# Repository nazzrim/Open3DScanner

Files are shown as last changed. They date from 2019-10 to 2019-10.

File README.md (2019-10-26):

# Open3DScanner
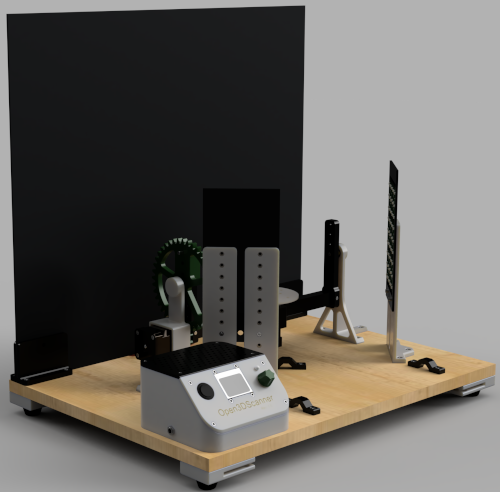
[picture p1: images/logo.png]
The Open3DScanner


The Open3DScanner is an open source photogrammetry 3D Scanner. Despite its name it does not provide you with the full photogrammetry pipeline.

Instead it enables you to automaticall create sets of photos by using your smartphone camera. These photos need to be processed by your normal photogrammetry pipeline later on.

But by automating the process of capturing the required photos the time you need to spend on creating a 3D scan can significantly decreased.

## Features
- Automatic generation of photosets for photogrammetry
- Support for android and iOS devices
- Adjustable scanning parameters for different granularities of detail
- Integrated LED lights to increase illumination of photos
- Removable backplate and storage area below the baseplate for reduces space requirements
- Adjustable scanner frame for differently sized objects
- Extensive documentation, providing you with build instructions and many additional informations about photogrammetry, the design process, and other open source 3D scanners

## License
Since this repository contains mixed resources (code, documents, images, ...) thera are different licenses which apply to different portions of the repository.

For that reason each subfolder of the root folder contains its own LICENSE.md file which defines the license which applies to the corresponding resources.

But in general code and 3D model resources are licensed under the GPLv3 while media resources (like documents and images) are licensed with the CC-BY-SA 4.0 license.

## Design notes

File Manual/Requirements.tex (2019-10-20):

\chapter{Required Parts}%
\label{c:bom}%
This chapter shows which things are needed to build the Open3DScanner. It looks at the components of the printer as well as the tools and devices needed to assemble it.%

It is recommended to read this chapter carefully if you want to build your own Open3DScanner.%

\section{Bill of Materials}%
One of the most important points to build your own Open3DScanner is a bill of materials of the required parts.%

This is contained in the following sections. The complete list is divided into two partial lists. The first one contains all electrical components which can be found on the PCB or are connected to it. The second list contains all further things that are needed to assemble the Open3DScanner.%

\subsection{Electrical Components}%
The following table contains all electrical components required to build the Open3DScanner.%

In addition to the component and the required quantity, the identifier of the respective component on the circuit board is also specified. In addition to this, information is given for individual components, which must be considered when purchasing.%

\begin{table}[ht!]%
	\begin{centered}%
		\rowcolors{2}{tableLineTwo}{tableLineOne}% specify rowcolors in tabularx style
		\begin{tabularx} {\linewidth} {>{\rowmac \hsize=1.4\hsize}X>{\rowmac \hsize=0.3\hsize}X>{\rowmac \hsize=0.6\hsize}X>{\rowmac \hsize=1.7\hsize}X<{\clearrow}}%
			\tabularxHeader%
			Component & Quantity & PCB-Identifier  & Note\\%
			\hrefIdx{https://www.espressif.com/en/products/hardware/esp32-devkitc/overview}{ESP32-DevKitC} & 1 & A1 & While I use the \hrefIdx{https://www.az-delivery.de/products/esp32-developmentboard}{AZ-Delivery ESP32-DevKitC}, any version that meets the \hrefIdx{https://www.espressif.com/en/products/hardware/esp32-devkitc/overview}{ESP32-DevKitC} specification should work.\\%
			\hrefIdx{https://www.pololu.com/product/1182}{A4988 Stepper Driver} & 2 & A2TT1 \& A3RT1 & Any A4988 steper driver should work. I recommend getting matching heat sinks.\\%
			\hrefIdx{https://reprap.org/wiki/NEMA\_17\_Stepper\_motor}{Nema 17 Stepper Motor} & 2 & M1RT1 \& M2TT1 & Make sure to buy the version with D-shaft. I use strong stepper motors, like this \hrefIdx{https://www.omc-stepperonline.com/nema-17-stepper-motor/nema-17-bipolar-59ncm-84oz-in-2a-42x48mm-4-wires-w-1m-cable-and-connector-full-d-cut-shaft.html}{\SI{59}{\newton\centi\meter} Nema 17 stepper motor}.\\%
			\hrefIdx{https://www.analog.com/en/products/lt1086.html}{LT1086CT-5} & 1 & U2 & Ensure to get the \hrefIdx{https://www.centralsemi.com/PDFS/CASE/TO\_220\_PD.PDF}{TO-220} type.\\%
			\hrefIdx{https://www.infineon.com/cms/en/product/power/mosfet/12v-300v-n-channel-power-mosfet/irlb8721/}{IRLB 8721} & 1 & Q1 & Ensure to get the \hrefIdx{https://www.centralsemi.com/PDFS/CASE/TO\_220\_PD.PDF}{TO-220} type.\\%
			TO-220 Heatsink & 2 & Q1 \& U2 & I highly recommend at least one for the \hrefIdx{https://www.analog.com/en/products/lt1086.html}{LT1086CT-5} since it gets very hot during operation. The one for the \hrefIdx{https://www.infineon.com/cms/en/product/power/mosfet/12v-300v-n-channel-power-mosfet/irlb8721/}{IRLB 8721} is just to be safe. While I am using the \hrefIdx{https://www.fischerelektronik.de/web\_fischer/en\_GB/heatsinks/C02/Attachable\%20heatsink/PG/FK245MI247O/search.xhtml}{FK 245 MI 247 O} you can choose whatever fits in the space (about \SI{22.5}{\milli\meter}$\times$\SI{10}{\milli\meter}).\\%
			\SI{1}{\milli\litre} Thermal Paste & 1 & - & Required for a good connection between \hrefIdx{https://www.centralsemi.com/PDFS/CASE/TO\_220\_PD.PDF}{TO-220} components and their heatsink. Only a tiny amount is required.\\%
			\hrefIdx{https://www.alps.com/prod/info/E/HTML/Encoder/Incremental/EC12E/EC12E\_list.html}{STEC12E08 Rotary Encoder} & 1 & - & This will be connected to the pin header SW1.\\%
			\hrefIdx{https://www.sparkfun.com/products/10168}{Nokia 5110 Display} & 1 & - & This will be connected to the pin header DS1. Buy one with screw holes. Hole distance on x-axis should be \SI{34}{\milli\meter} and \SI{40.5}{\milli\meter} on the y-axis.\\%
			\SI{5}{\milli\meter} 3-Pin Bi-Color LED & 1 & - & This will be connected to the pin header D1. I recommend using a red-green one.\\%
			\SI{5}{\meter}$\times$\SI{8}{\milli\meter} 300 LED 3528 Strip, \SI{12}{\volt} \SI{1.5}{\ampere} & 1 & - & This will be connected to the pin headers D2, D3, D4, D5.\\%
			Round \SI{20}{\milli\meter} SPST Rocker Switch (R13 112) & 1 & - & This will be connected to the pin header SW2.\\%
			\SI{5.5}{\milli\meter}$\times$\SI{2.1}{\milli\meter} Female DC Power Jack Panel Mount (L722AS) & 1 & - & This will be connected to the pin header SW2. Make sure to grab one with threads and a nut for panel mounting.\\%
			\SI{473}{\nano\farad} Ceramic Capacitor & 1 & C3 & Choose \SI{2.54}{\milli\meter} pin distance and \SI{3.4}{\milli\meter} radius.\\%
			\SI{10}{\micro\farad} Electrolytic Capacitor & 1 & C1 & Choose \SI{2}{\milli\meter} pin distance and \SI{4}{\milli\meter} radius.\\%
			\SI{100}{\micro\farad} Electrolytic Capacitor & 3 & C2, C4, C5 & Choose \SI{2.5}{\milli\meter} pin distance and \SI{6.3}{\milli\meter} radius.\\%
			\SI{100}{\ohm} Resistor & 3 & R1, R2, R6 & Choose whatever you have at hand, like carbon film or metal (oxide) film.\\%
			\SI{330}{\ohm} Resistor & 1 & R4 & Choose whatever you have at hand, like carbon film or metal (oxide) film.\\%
			\SI{10}{\kilo\ohm} Resistor & 2 & R3, R5 & Choose whatever you have at hand, like carbon film or metal (oxide) film.\\%
		\end{tabularx}%
		\caption{BOM for all electrical components of the Open3DScanner --- Part 1/3}%
	\end{centered}%
\end{table}%
\begin{table}[ht!]%
	\begin{centered}%
		\rowcolors{2}{tableLineTwo}{tableLineOne}% specify rowcolors in tabularx style
		\begin{tabularx} {\linewidth} {>{\rowmac \hsize=1.4\hsize}X>{\rowmac \hsize=0.3\hsize}X>{\rowmac \hsize=0.6\hsize}X>{\rowmac \hsize=1.7\hsize}X<{\clearrow}}%
			\tabularxHeader%
			Component & Quantity & PCB-Identifier  & Note\\%
			\hrefIdx{https://www.sparkfun.com/products/8432}{2-Pin Screw Terminals 5mm Pitch} & 7 & J1, J2, SW2, D2, D3, D4, D5 & Take care to get the ones with 5mm pitch.\\%
			\SI{2.54}{\milli\meter} 40-Pin Header & 1 & M1RT1, M2TT2, D1, DS1, SW1 & Will be cut into 1$\times$3, 2$\times$4, 1$\times$5, and 1$\times$8.\\%
			\SI{2.54}{\milli\meter} 40-Pin Socket & 2 & A1, A2TT1, A3RT1 & Will be cut into 2$\times$19 and 4$\times$8. Each cut results in one socket loss.\\%
			1$\times$3 Dupont Housing & 4 & - & Will be used to connect D1 with the bi-color LED on both sides as well as the STEC12E08 rotary encoder on component side.\\%
			1$\times$5 Dupont Housing & 1 & - & Will be used to connect SW1 with the rotary encoder on PCB side.\\%
			1$\times$8 Dupont Housing & 2 & - & Will be used to connect DS1 with the LCD on both sides.\\%
			Female Dupont Terminals & 33 & - & Required for all Dupont housings.\\%
			Molex crimp housing --- Micro-Fit - 1x2-pin, male (430200201) & 4 & - & Required for connecting the lights to the Open3DScanner. Part number \hrefIdx{https://www.molex.com/molex/products/datasheet.jsp?part=active/0430200201\_CRIMP\_HOUSINGS.xml}{Molex 430200201}\\%
			Molex crimp housing --- Micro-Fit - 1x2-pin, female & 4 & - & Required for connecting the lights to the Open3DScanner. Part number \hrefIdx{https://www.molex.com/molex/products/datasheet.jsp?part=active/0430250200\_CRIMP\_HOUSINGS.xml}{Molex 430250200}\\%
			Molex crimp contact --- Micro-Fit, female  & 8 & - & Required for connecting the lights to the Open3DScanner. Part number \hrefIdx{https://www.molex.com/molex/products/datasheet.jsp?part=active/0430300007\_CRIMP\_TERMINALS.xml}{Molex 430300007}\\%
			Molex crimp contact --- Micro-Fit, male  & 8 & - & Required for connecting the lights to the Open3DScanner. Part number \hrefIdx{https://www.molex.com/molex/products/datasheet.jsp?part=active/0430310007\_CRIMP\_TERMINALS.xml}{Molex 430310007}\\%
			Cable Lug & 4 & - & The cable lugs have to match your power jack and your rocker switch. For me it is 2$\times$\SI{2.8}{\milli\meter} (power jack) and 2$\times$\SI{4.8}{\milli\meter} (rocker switch).\\%
			Power Supply \SI{12}{\volt}, \SI{2250}{\milli\ampere} with \SI{5.5}{\milli\meter}$\times$\SI{2.1}{\milli\meter} male Barrel Jack & 1 & - & This will power the whole Open3DScanner\\%
			\SI{15}{\centi\meter} Micro USB-B cable & 1 & - & Used to connect J2 with the ESP32's usb port. Get an already prepared cable if you can, otherwise you need to cut one yourself.\\%
			AWG 18 or \SI{0.75}{\milli\meter\squared} cable & - & - & Used for transmitting power (e.g. from power jack to PCB, within pieces of the LED strip, and towards the LED strip). Since the cables are not exposed to any or only little movement, no special requirements like silicone cables exist. I use simple speaker cable which is sold in rolls of \SI{25}{\meter}. I cannot provide an accurate required quantity for the wires since it depends somewhat on individual wiring.\\%
		\end{tabularx}%
		\caption{BOM for all electrical components of the Open3DScanner --- Part 2/3}%
	\end{centered}%
\end{table}%
\begin{table}[ht!]%
	\begin{centered}%
		\rowcolors{2}{tableLineTwo}{tableLineOne}% specify rowcolors in tabularx style
		\begin{tabularx} {\linewidth} {>{\rowmac \hsize=1.4\hsize}X>{\rowmac \hsize=0.3\hsize}X>{\rowmac \hsize=0.6\hsize}X>{\rowmac \hsize=1.7\hsize}X<{\clearrow}}%
			\tabularxHeader%
			Component & Quantity & PCB-Identifier  & Note\\%
			AWG 24 or \SI{0.2}{\milli\meter\squared} cable & - & - & Used to connect the various components to the PCB. I cannot provide an accurate required quantity for the wires since it depends somewhat on individual wiring.\\%
			PCB & 1 & - & The Gerber files for the PCB of the Open3DScanner are part of this project and can be used to get PCBs from a manufacturer.\\%
		\end{tabularx}%
		\caption{BOM for all electrical components of the Open3DScanner --- Part 3/3}%
	\end{centered}%
\end{table}%

\subsection{Other Components}%
The previous section contains the BOM for all electrical parts of the Open3DScanner.%

In addition, this section contains a BOM for all remaining parts needed to build the Open3DScanner. The separation should help to better bundle the orders with the respective suppliers.%

It should be noted that the quantities specified for the screws indicate maximum quantities. These can be smaller, e.g. if the maximum of four lights are not mounted.%

\begin{table}[ht!]%
	\begin{centered}%
		\rowcolors{2}{tableLineTwo}{tableLineOne}% specify rowcolors in tabularx style
		\begin{tabularx} {\linewidth} {>{\rowmac \hsize=1.2\hsize}X>{\rowmac \hsize=0.3\hsize}X>{\rowmac \hsize=1.5\hsize}X<{\clearrow}}%
			\tabularxHeader%
			Component & Quantity & Note\\%
			\SI{400}{\milli\meter} $\times$ \SI{550}{\milli\meter} $\times$ \SI{16}{\milli\meter} Wooden Board & 1 & This will be used as the base of the whole Open3DScanner\\%
			\SI{500}{\milli\meter} $\times$ \SI{550}{\milli\meter} $\times$ \SI{3}{\milli\meter} PVC Rigid Foam Sheet & 1 & The rear panel of the Open3DScanner.\\%
			\SI{800}{\gram} Roll ABS Filament & 1 & Main color. Other materials like PLA may be fine.\\%
			\SI{800}{\gram} Roll ABS Filament & 1 & Secondary color. Other materials like PLA may be fine.\\%
			\SI{800}{\gram} Roll ABS Filament & 1 & Accent color. Other materials like PLA may be fine.\\%
			Nema 17 Damper & 2 & For decoupling the motors from the Open3DScanner's structure.\\%
			Liquid Glue & 1 & Required for assembling the lights if the M3 tape which is applied to the LED strip does not hold and to glue some nuts in place.\\%
			\SI{5}{\milli\meter} $\times$ \SI{26}{\milli\meter} Steel Rod & 5 & Used to connect and secure various parts.\\%
			625ZZ Bearing & 2 & Used to connect the moving parts to the frame with as little friction as possible.\\%
		\end{tabularx}%
		\caption{BOM for all non-electrical components of the Open3DScanner 1/2}%
	\end{centered}%
\end{table}%

\begin{table}[ht!]%
	\begin{centered}%
		\rowcolors{2}{tableLineTwo}{tableLineOne}% specify rowcolors in tabularx style
		\begin{tabularx} {\linewidth} {>{\rowmac \hsize=1.2\hsize}X>{\rowmac \hsize=0.3\hsize}X>{\rowmac \hsize=1.5\hsize}X<{\clearrow}}%
			\tabularxHeader%
			Component & Quantity & Note\\%
			M3$\times$6 SHCS & 6 & Used to connect the stepper motors to the dampers as well as the LED to the housing.\\%
			M3$\times$8 SHCS & 12 & Used for various connections.\\%
			M3$\times$10 SHCS & 12 & Used for various connections.\\%
			M3$\times$12 SHCS & 6 & Used for various connections.\\%
			M3$\times$20 SHCS & 4 & Used for various connections.\\%
			M3 Nut & 40 & Used for assembling the lights.\\%
			4.0$\times$16 Countersunk Wood Screw & 56 & Used to connect the individual parts with the base.\\%
			5/8'' Rubber Seal Ring & 1 & Used for the stepper driver cable entry in the housing.\\%
			\SI{30}{\milli\meter} $\times$ \SI{15}{\milli\meter} Rubber Feet & 4 & Used as feet for the Open3DScanner.\\%
		\end{tabularx}%
		\caption{BOM for all non-electrical components of the Open3DScanner 2/2}%
	\end{centered}%
\end{table}%

\section{Used Tools}%
Various tools are required to set up the Open3DScanner. These are described in this section.%

At first the standard tools are listed, which are needed, but are not described in this chapter. Screwdrivers are needed for the used screws and even if pliers and tweezers are not absolutely necessary, they prove to be useful in some parts of the assembly.%

\subsection{3D Printer}%
A 3D printer is needed to print all the models from which the Open3DScan-ner is built. The requirements are relatively low as all parts can be printed from PLA or ABS\marginInfo[Used Filaments]{I printed all parts for the Open3DScanner with ABS, so it's the only material I can say for sure that it works. However, it should be possible to use PLA and PETG, as well as other materials, as there are no special forces acting on the parts.}.%

All parts have been designed to fit in the print volume of an \hrefIdx{https://www.prusa3d.com/original-prusa-i3-mk3/}{Original Prusa i3 MK3}, which has a print volume of \SI{250}{\milli\meter} $\times$ \SI{210}{\milli\meter} $\times$ \SI{210}{\milli\meter}. Any other FDM 3D printer can be used, which has at least this print volume. The only thing I am recommending is a heated printing bed, but nowadays it is included in almost all printers.%

\subsection{Crimping Tools}%
In order to achieve a decent and secure wiring of the Open3DScanner, it is necessary to crimp the cables.%

Different crimping tools are used for the different connections. A ferrule crimper is used for the connections to the screw terminals, a universal crimping tool\marginTips[Universal Crimper]{While I mostly bought cheap sets for my crimping tools, I bought an \hrefIdx{http://www.engineer.jp/en/products/pa09e.html}{Engineer PA-09} for crimping Dupont cables, because I crimp such cables most often. Even if this crimping tool is a bit more expensive than comparable crimping pliers, the quality of the crimping tool pays off. For this reason I recommend the \hrefIdx{http://www.engineer.jp/en/products/pa09e.html}{Engineer PA-09}, especially if you frequently crimp Dupont cables.} is used for the dupont cables, which connect the individual components to the board, and a terminal crimp tool is used for the connections to individual components, which have plugs for cable lugs.%

\subsection{Soldering Iron}%
A soldering iron is required to assemble the board. Since the Open3DScan-ner does not use any particularly sensitive or otherwise special parts, almost any soldering iron can be used. It is not necessary to use a digital soldering station.%

\section{Hardware for Photogrammetry}%
A powerful computer shortens the necessary processing time for the photogrammetry process. As already mentioned in chapter~\ref{sec:photogrammetry}, a Nvidia GPU is required to use the Meshroom software. Other photogrammetry software may not require a Nvidia GPU.%

Otherwise, photogrammetry software benefits greatly from more RAM, which is why \SI{32}{\giga\byte} is a reasonable lower limit, which is also mentioned by various manufacturers of software for photogrammetry.%

A further important point that must be considered is that during the calculation large amounts of data are generated in the individual intermediate steps, which have to be persisted. The size of the generated data exceeds the size of the input images by a multiple. One of my example scans with 231 images generated over \SI{20}{\giga\byte}\marginInfo[Example Scan]{The mentioned scan consists of four individual scans, whose data were combined. At this point we do not want to go into further detail regarding this scan, corresponding information can be found in the chapters~\ref{c:userGuide} and~\ref{c:performingScans}.} of data.%

For this reason it must be ensured that sufficiently large amounts of storage space are available.%

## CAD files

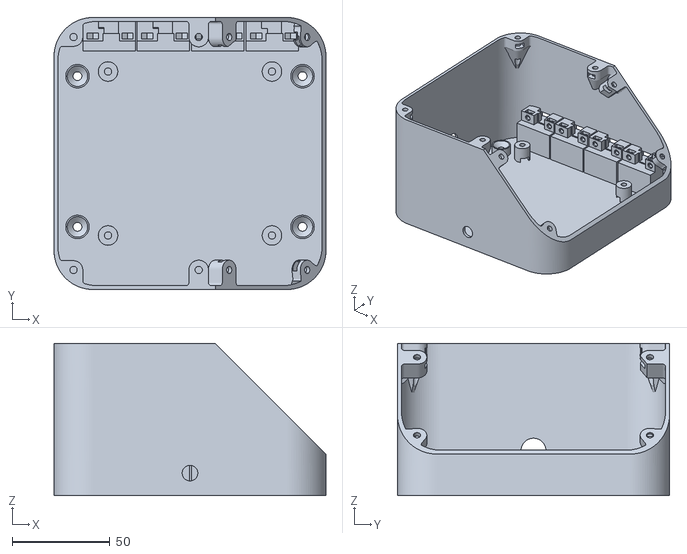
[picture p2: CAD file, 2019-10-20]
STLs/Housing/Housing-Main_v1.stl
139.1 x 139.1 x 77.8

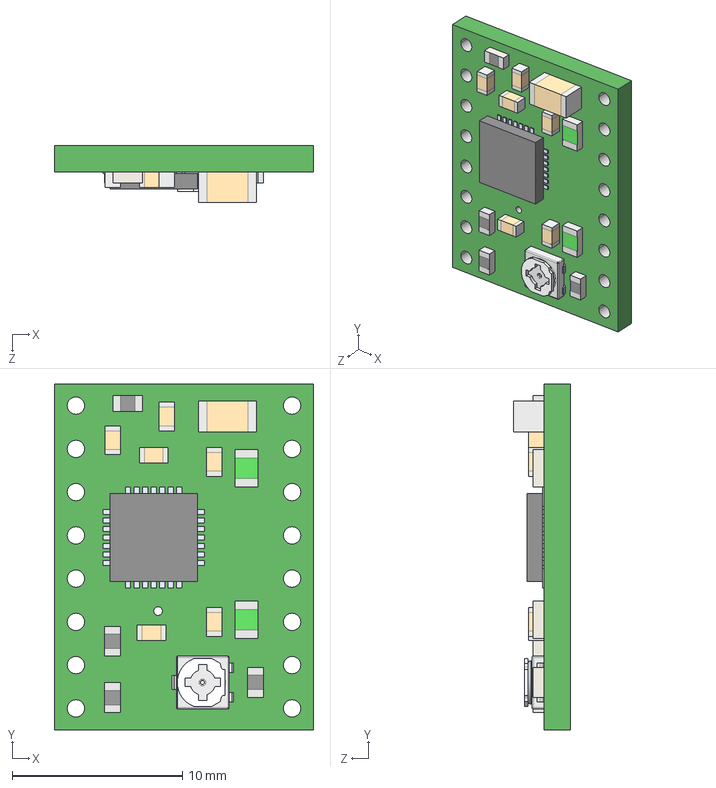
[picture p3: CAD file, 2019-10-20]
PCB/3D Models/a4988-stepper-motor-driver-carrier.step
15.2 x 20.3 x 3.37 mm

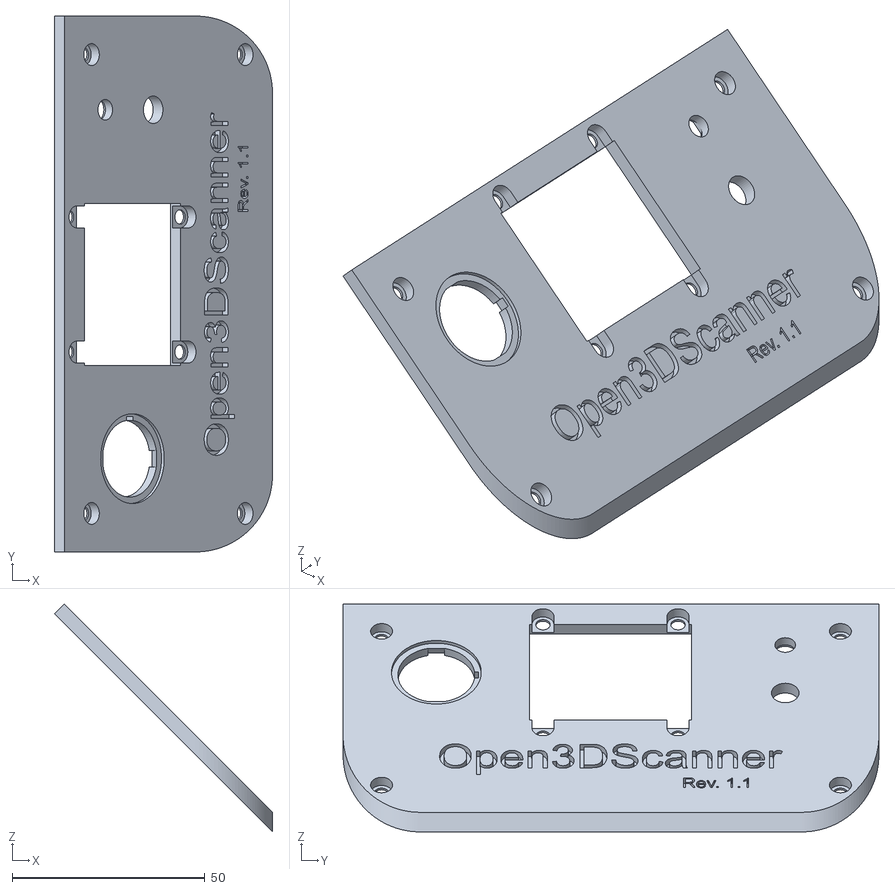
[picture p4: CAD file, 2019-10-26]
STLs/Housing/Housing-Plate_v1.stl
56.6 x 139.1 x 59.1

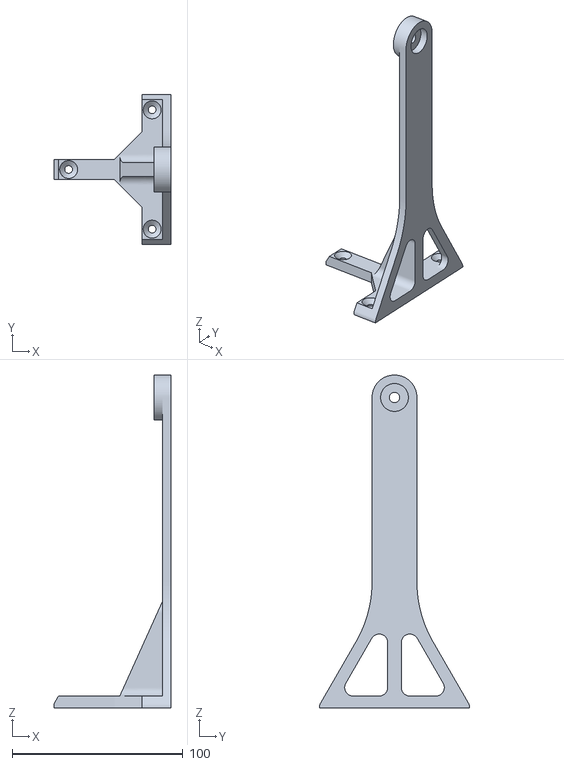
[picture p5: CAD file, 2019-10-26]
STLs/Passive-Stand_v1.stl
68.5 x 88.1 x 195.2

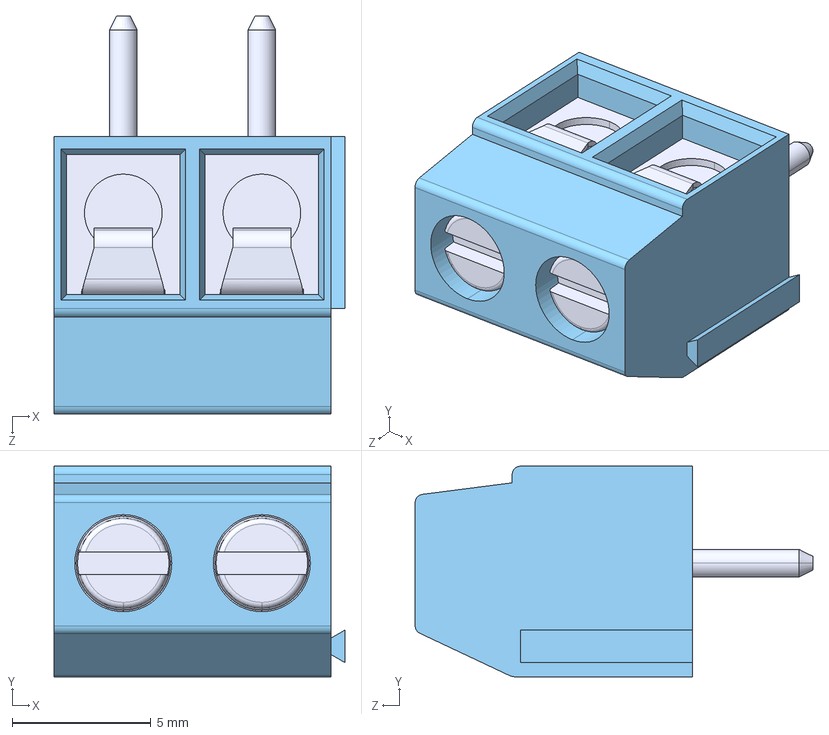
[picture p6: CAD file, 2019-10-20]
PCB/3D Models/CUI_TB002-500-02BE.step
10.5 x 7.60 x 14.4 mm

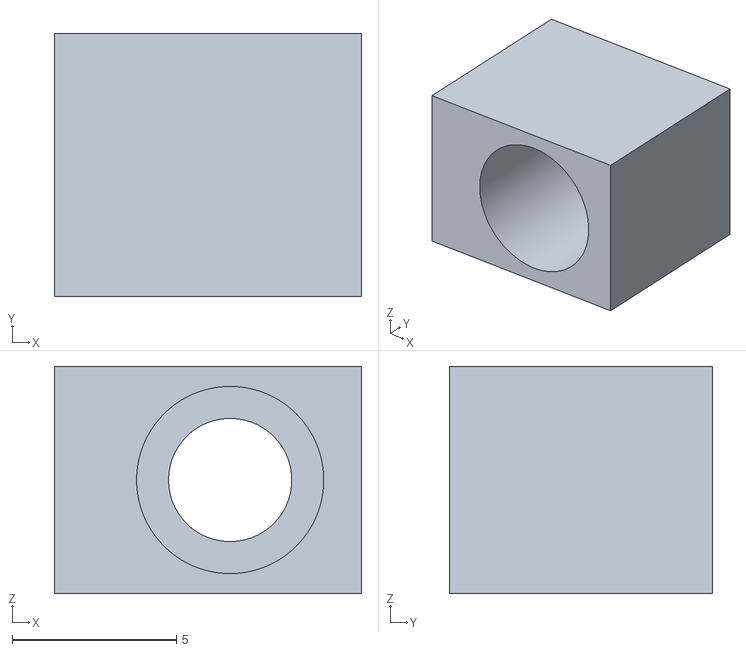
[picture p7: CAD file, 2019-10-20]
STLs/Housing/MicroFit-Holder-P2_v1.stl
9.35 x 8.00 x 6.93

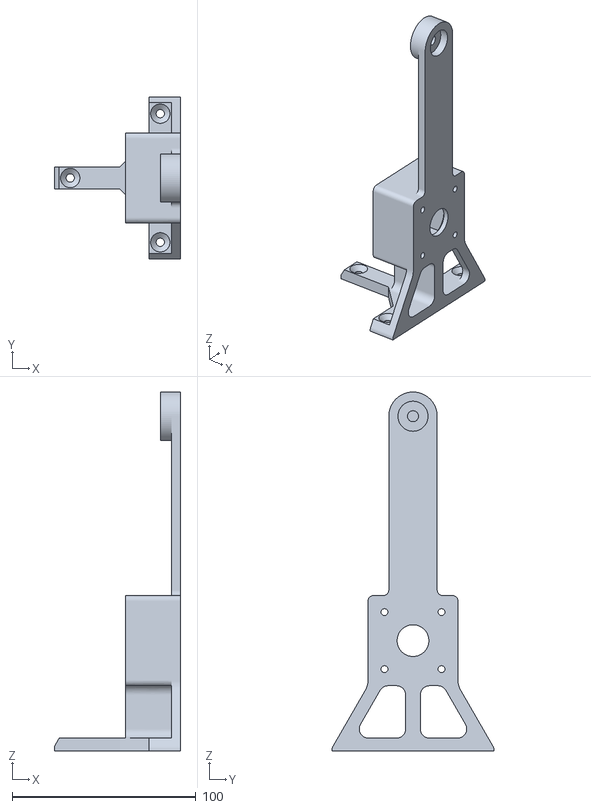
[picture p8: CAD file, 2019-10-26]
STLs/Rotor-Stand_v1.stl
68.5 x 88.1 x 195.2

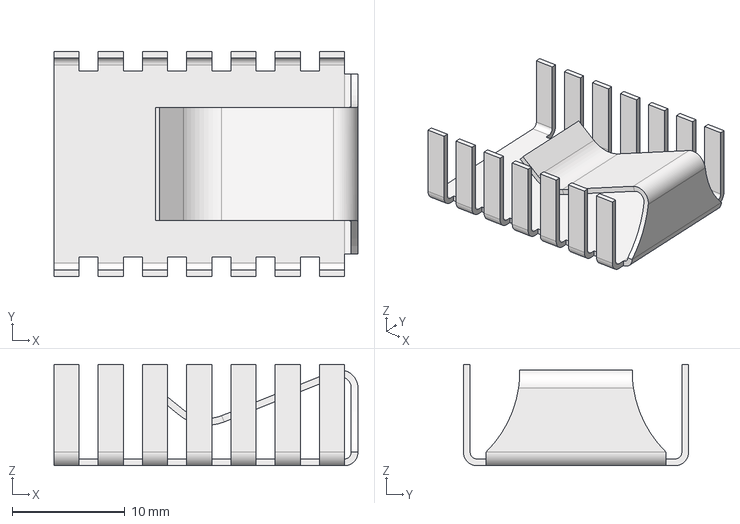
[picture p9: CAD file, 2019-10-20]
PCB/3D Models/fk_245_mi_247_o.stp
27.0 x 20.0 x 9.00 mm

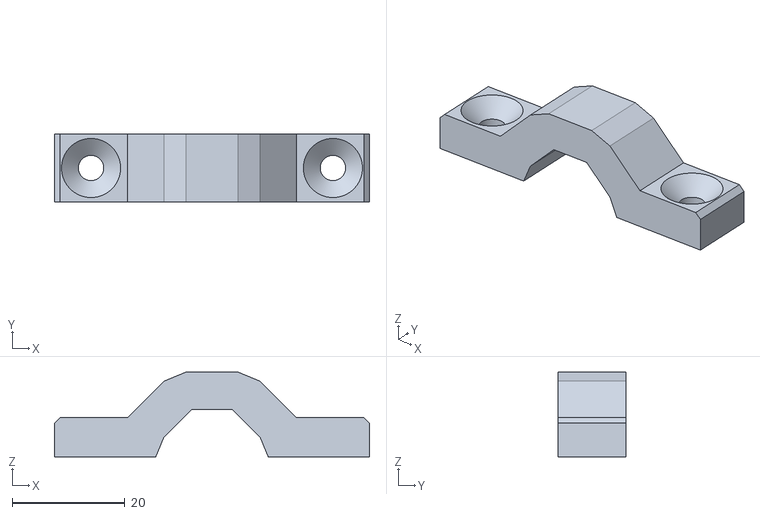
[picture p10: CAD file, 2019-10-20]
STLs/Cable-Holder_v1.stl
56.0 x 12.0 x 15.1

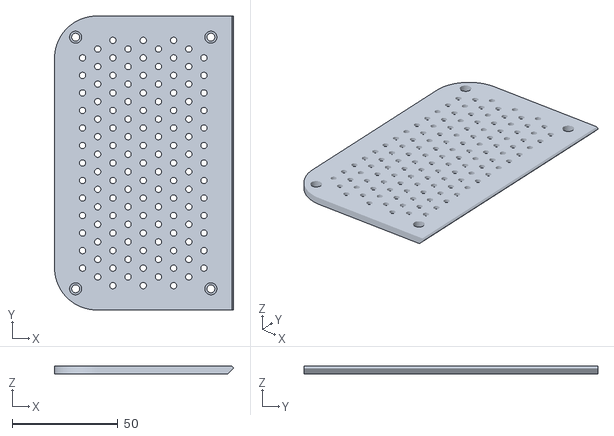
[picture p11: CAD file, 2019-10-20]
STLs/Housing/Housing-Top_v1.stl
84.7 x 139.1 x 3.60

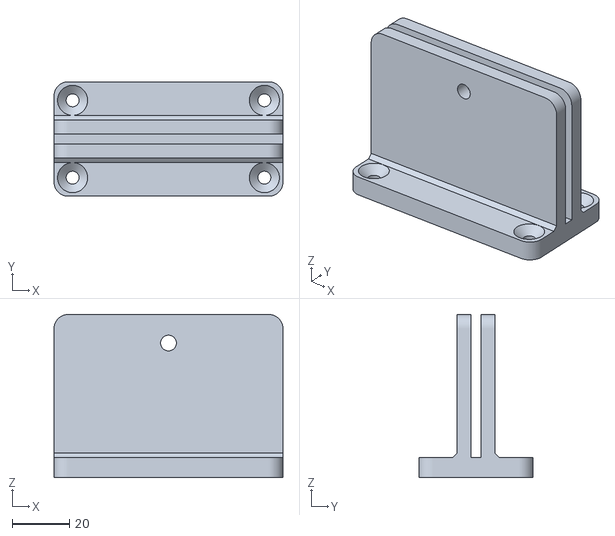
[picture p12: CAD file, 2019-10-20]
STLs/Backplate-Holder_v1.stl
80.0 x 40.0 x 57.0

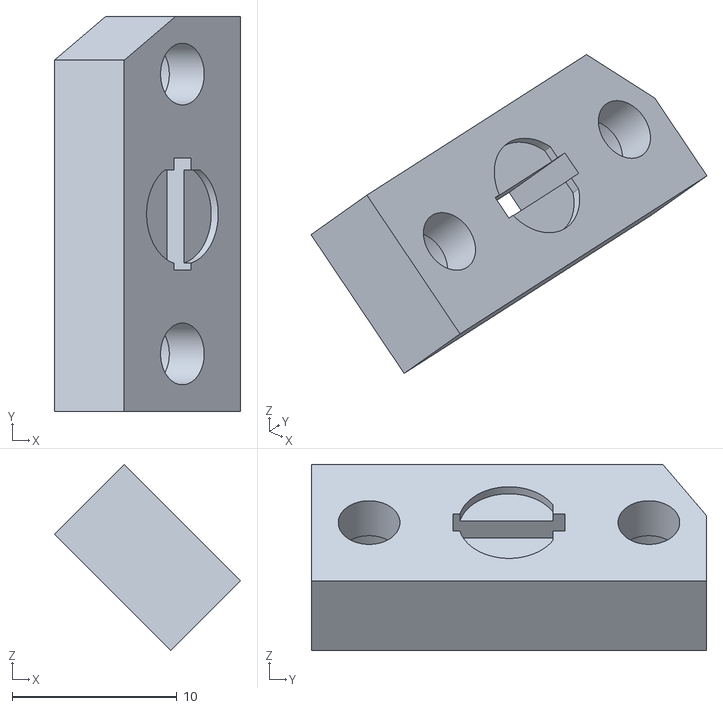
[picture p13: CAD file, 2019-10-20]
STLs/Housing/LED-Holder_v1.stl
11.3 x 24.0 x 11.3

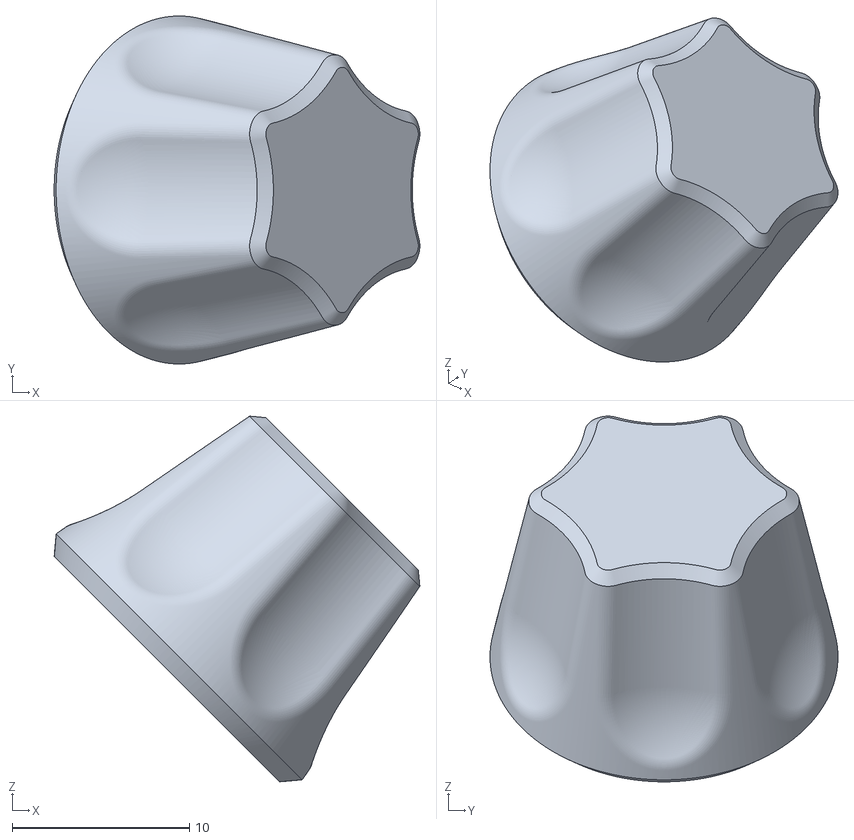
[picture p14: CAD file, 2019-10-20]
STLs/Housing/Knob_v1.stl
20.7 x 19.7 x 20.7

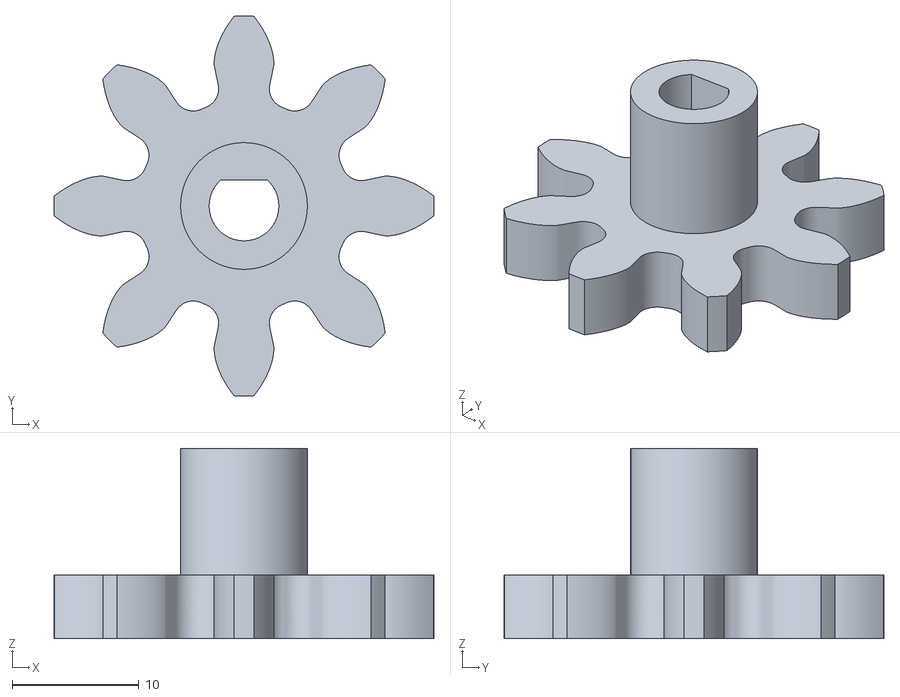
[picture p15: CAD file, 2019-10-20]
STLs/Rotor-Pinion_v1.stl
30.0 x 30.0 x 15.0

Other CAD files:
STLs/Rotor-Arm_v1.stl
STLs/Housing/Encoder-Holder_v1.stl
STLs/Turntable-Arm_v1.stl
STLs/Housing/LCD-Holder_v1.stl
STLs/Foot-Holder-Clamp_v1.stl
STLs/Housing/MicroFit-Holder-P1_v1.stl
STLs/Rotor-Gear_v1.stl
STLs/Spotligt-Frame_v1.stl
STLs/Spotligt-Stand_v1.stl
STLs/Turntable-Medium_v1.stl

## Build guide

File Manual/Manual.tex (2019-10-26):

\documentclass[a4paper]{yReport}%

\usepackage{fontawesome5}% Required by yAuthorBlock
\usepackage{yAuthorBlock}% Used to create the author block on page 2
\usepackage{tabularx}% Since tabu (used by yReport) is not behaving the expected way, use tabularx
\usepackage[binary-units=true]{siunitx}% Used to display numbers and units in a proper way
\usepackage{indextools}% Used to build a href list for printed documents
\usepackage{xparse}% Required for string magic to display urls in index a proper way
\usepackage{infoBulle}% Necessary to display the info/warn/... blocks in the main area
\usepackage{marginInfoBulle}% Necessary to display the info/warn/... blocks in the margin area
\usepackage[cleanlook, english, TeX]{isodate}% Used for uniform displaying dates. Required because of strange behaviour of datetime package (included in yReport)
\usepackage{xurl}% Override url command do allow linebreaks everywhere
\usepackage{hologo}% Used to disaplay logos from the latex family

\definecolor{mainColor}{RGB}{39, 174, 96}% Main color used for decorations --> nephretis
\definecolor{secondColor}{RGB}{142, 68, 173}% Secondary color used for e.g. links --> wisteria

\newcommand{\urlCheckedOne}{\origdate\printdateTeX{2019/10/20}\TeXdate}% Date variables
\newcommand{\releaseOne}{\printdateTeX{2019/10/20}}%
\newcommand{\releaseTwo}{\printdateTeX{2019/10/26}}%

\input{Commands}% This file contains 'messy' configuration which would make this file less readable

\author{Nazrim}%
\subtitle{Manual --- Rev. 1.1}%
\title{Open3DScanner}%

\hypersetup{%
	pdftitle={Open3DScanner},%
	pdfsubject={Manual --- Rev. 1.1},%
	pdfauthor={Nazrim},%
	pdfkeywords={{3D Scanner}{Open Source}{Open Hardware}{Photogrammetry}{Arduino}{ESP32}},%
}%

\makeatletter%
\let\runauthor\@author%
\let\runtitle\@title%
\makeatother%

\begin{document}%
	\startcontents[content]% Ensure function of Toc
	\titleThree[images/cover]% Build title page
	\chaptermark{License}% Create valid header on toc/license/author side
	\printMarginToc[1][Table of contents]% Print toc in margin
	
	\sideTabularx[History of this document]{%
		\begin{tabularx} {\marginparwidth} {>{\rowmac \hsize=.6\hsize}X>{\rowmac}X>{\rowmac \hsize=1.4\hsize}X<{\clearrow}}%
			\tabularxHeader%
			Version & Date & Note\\%
			1.0 & \releaseOne & Initial release\\%
			1.1 & \releaseTwo & Minior bugfixes\\%
		\end{tabularx}%
	}%

	\section*{License}%
		This document is licensed under the Creative Commons At\-tri\-bu\-tion-Share\-Alike 4.0 International License. To view a copy of this license, visit \url{https://creativecommons.org/licenses/by-sa/4.0/}.%
	
	\vfill%
	\authorBlock{%
		\authorName{Nazrim}%
		\authorWebsite{https://www.myminifactory.com/users/Nazrim}[\faCubes]%
		\authorWebsite{https://www.thingiverse.com/Nazrim}[\faCubes]%
		\authorWebsite{https://www.hackster.io/Nazrim}[\faCubes]%
		\authorWebsite{https://github.com/nazzrim}[\faGithub]%
	}%
	\include{Introduction}%
	\include{RelatedProjects}
	\include{References}%
	\include{Requirements}%
	\include{BuildInstructions}%
	\include{UserGuide}%
	\include{PerformingScans}%
	\appendix% start appendices
	\include{AppendixPCB}
	\indexprologue{%
		\label{ca:refs}%
		In case the document is available in printed form, this chapter contains all used links, which are provided with alternative display texts. This also allows these references to be followed.%
		
		The references are sorted alphabetically and not according to their appearance in the document.A few of the link texts are interpreted as special characters (e.g. \hologo{XeLaTeX}), so they do not appear at the expected position of the index, but at the beginning.%
		
		All links listed in this appendix were checked for validity on \urlCheckedOne.%
	}%
	\printindex[hrefs]%
\end{document}%

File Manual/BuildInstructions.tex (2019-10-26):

\chapter{Build Instructions}%
\label{c:build}%
This chapter explains step by step the individual steps that are necessary to build an Open3DScanner from the individual components.%

The individual work steps are grouped together to summarize similar tasks.%

\section{Printing the Parts}%
First, the required parts must be printed for assembly. As mentioned before, I recommend using ABS filament as it's the only type of filament I've tested for the Open3DScanner, but I assume that other materials like PLA and PETG will work as well.%

So just use PLA if you can't print ABS with your 3D printer, for example because you don't have a closed print area or a heated print bed.%

The parts of the Open3DScanner were designed so that they all fit into the print volume of an \hrefIdx{https://www.prusa3d.com/original-prusa-i3-mk3/}{Original Prusa i3 MK3} (at least individually). This ensures that most 3D printers are able to print the parts for the Open3DScanner.%

The tolerance for the connections between the parts, as well as for screw holes etc. is \SI{0.35}{\milli\meter} for all parts at all points\marginTips[Test print]{It may be helpful to print a part as a sample and check that the tolerances used are appropriate for the printer being used.}.%

With the exception of the Rotor-Stand and Passive-Stand files, all files can be printed without support. For the two mentioned objects it is necessary to print support in the areas where the bearings are inserted. Apart from the removal of the support, no post-processing of the parts is necessary.%

\infoInfo{Note}{The assignment of the components to colours is arbitrary and corresponds to my personal taste. Of course it is possible to deviate from this "recommendation", it should only be pointed out that this allocation was used for the calculation of the necessary quantities of filament.}%

The following table lists which part has to be printed how often.%

\begin{table}[ht!]%
	\sideCaptionOf{table}{Quantity and color of 3D printed parts}%
	\rowcolors{2}{tableLineTwo}{tableLineOne}% specify rowcolors in tabularx style
	\begin{tabularx} {\linewidth} {>{\rowmac \hsize=\hsize}X>{\rowmac \hsize=\hsize}X>{\rowmac \hsize=\hsize}X<{\clearrow}}%
		\tabularxHeader%
		Part & Quantity & Color\\%
		Rotor-Arm  & 2 & Primary\\%
		Spotligt-Frame  & 1 --- 4 & Primary\\%
		Turntable-Arm  & 1 & Primary\\%
		Housing-Top  & 1 & Primary\\%
		Cable-Holder  & 5 & Primary\\%
		Backplate-Holder  & 2 & Primary\\%
		Turntable-Medium  & 1 & Secondary\\%
		Passive-Stand  & 1 & Secondary\\%
		Rotor-Stand  & 1 & Secondary\\%
		Spotligt-Stand  & 1 --- 4 & Secondary\\%
		Housing-Main  & 1 & Secondary\\%
		Housing-Plate  & 1 & Secondary\\%
		LCD-Holder  & 4 & Secondary\\%
		LED-Holder  & 1 & Secondary\\%
		Encoder-Holder  & 1 & Secondary\\%
		Micro-Fit-Holder-P1  & 4 & Secondary\\%
		Micro-Fit-Holder-P2  & 4 & Secondary\\%
		Food-Holder-Clamp  & 4 & Secondary\\%
		Rotor-Gear  & 1 & Accent\\%
		Rotor-Pinion  & 1 & Accent\\%
		Housing-Knob  & 1 & Accent\\%
	\end{tabularx}%
\end{table}%

% Primary: 477.30g
% Secondary: 810.67g
% Accent: 46.93g

The print settings for the objects are specified below. It is assumed that a \SI{0.4}{\milli\meter} nozzle is used. For other nozzles the values have to be adjusted accordingly.%

\begin{table}[ht!]%
	\sideCaptionOf{table}{Print settings for 3D printed parts with \SI[text-rm=\lightBoldFont]{0.4}{\milli\meter} nozzle}%
	\rowcolors{2}{tableLineTwo}{tableLineOne}% specify rowcolors in tabularx style
	\begin{tabularx} {\linewidth} {>{\rowmac \hsize=\hsize}X>{\rowmac \hsize=\hsize}X<{\clearrow}}%
		\tabularxHeader%
		Setting & Value\\%
		Layer height & \SI{0.2}{\milli\meter}\\%
		Perimeters & 4\\%
		Solid top layers & 5\\%
		Solid bottom layers & 5\\%
		Infill & \SI{40}{\percent}\\%
	\end{tabularx}%
\end{table}%

The amount of print settings listed in the table is kept as small as possible in order to describe only slicer independent settings.%

In particular, the use of a specific slicer is not necessary for successful printing. When selecting the remaining settings, it is only necessary to ensure that the printed objects are as stable as possible.%

The 3D models for the objects are all available in the orientation in which it is recommended to print them. The parts are aligned in such a way that the stability of the individual parts is improved under later loads (e.g. turntable arm) or that the quality of the printed details is improved in areas where this is important (e.g. spotlight frame).%

In case you stick to my color scheme and you build the maximum of four lights you will need a little bit over one \SI{800}{\gram} roll of filament of the secondary color. In total you need about \SI{500}{\gram} primary color filament, \SI{850}{\gram} secondary color filament, and \SI{80}{\gram} accent color filament.%

\section{Assembly the PCB}%
\label{sec:assPCB}%

This section describes how to assemble the PCB. This is not a step by step guide, but I pick up some special and important points and describe them.%

Such a step by step instruction for soldering the board is not included in this document. The only comparable one is a picture series, which documents all steps, which I have done during the assembly of the board. This picture series can be found in Appendix~\ref{cha:picSerPCB}.%

Instead, the board should be assembled in the way that is easiest for you. All components have an identifier, which can be found in the BOM and is printed on the PCB.%

\subsection{Preparing Pin Headers \& Sockets}%
Since both pin headers and pin sockets were purchased as 40 pin versions, it is necessary to cut the headers and sockets into suitable pieces before use.%

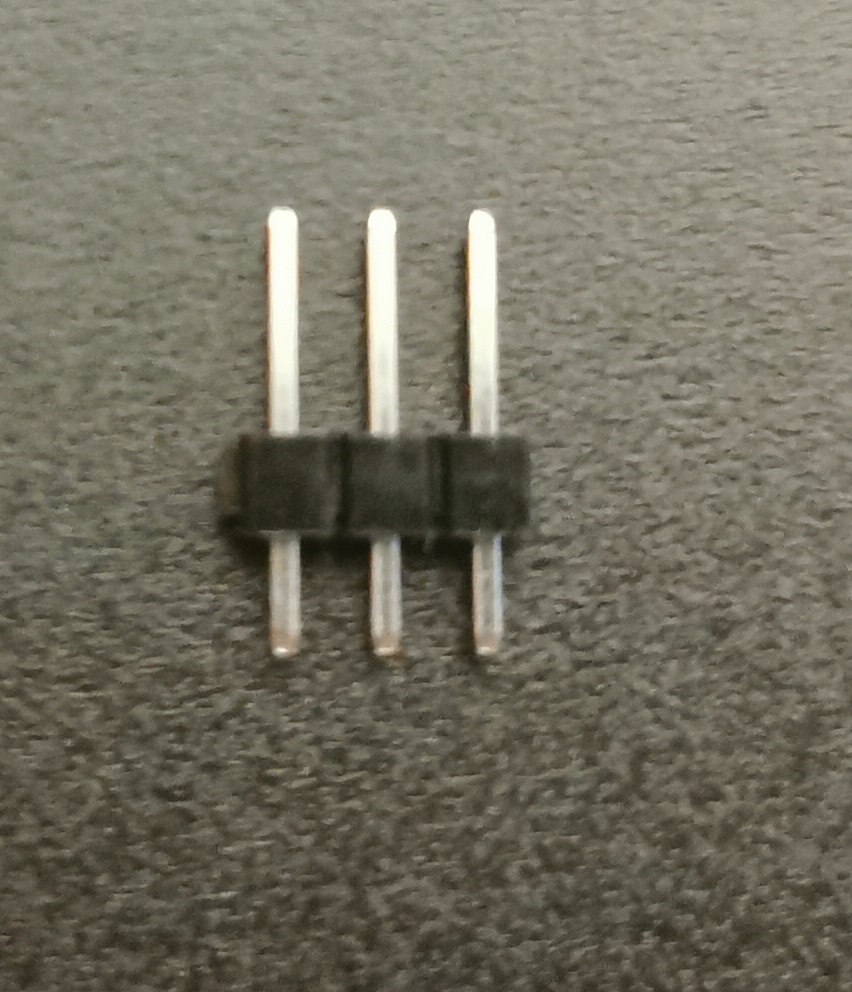
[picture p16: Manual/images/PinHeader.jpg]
\marginElement{\captionof{figure}{The notches between the pins simplify separation}\label{fig:pinHeader}}%

With the pin headers, the process is very simple, since there is always a notch between the pins where the headers can be separated with a side cutter. Figure~\ref{fig:pinHeader} shows a three pin header with the clearly visible notches.%

With pin sockets this process is not as easy as with pin headers. Because of missing space there are no notches between the pins.%

For this reason it is necessary to first remove a pin with pliers, at which the strip should be separated. If a five pin socket is needed, the sixth pin is removed. Afterwards the socket is cut carefully with a side cutter at the now free place. This allows the sockets to be separated safely and reliably. The rough edges can be smoothed with the side cutter. The process is shown in figure~\ref{fig:pinSocket}.%

\begin{figure}[ht!]%
	\begin{centered}%
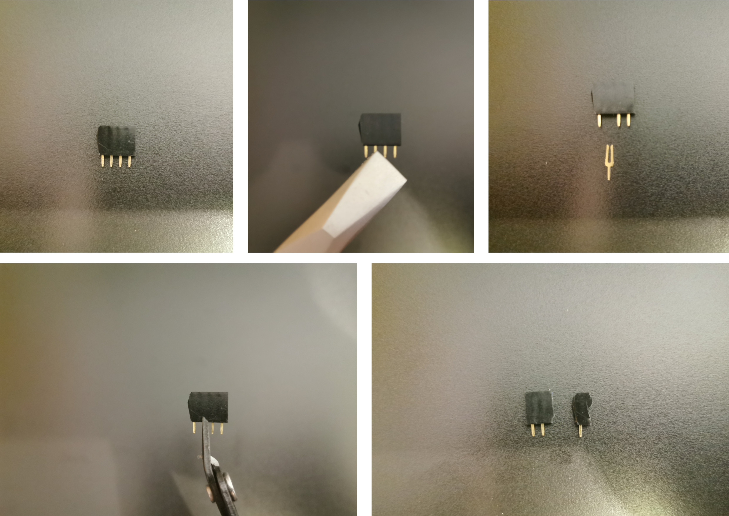
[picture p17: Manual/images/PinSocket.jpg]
		%
		\caption{How to separate pin sockets}%
		\label{fig:pinSocket}%
	\end{centered}%
\end{figure}%

\subsection{Assemble Pin Sockets}
The components which are mounted on pin sockets are the \hrefIdx{https://www.pololu.com/product/1182}{A4988 Stepper Drivers} and the \hrefIdx{https://www.espressif.com/en/products/hardware/esp32-devkitc/overview}{ESP32-DevKitC}.%

Both these components have two pin rows. It is therefore important that the pin sockets are mounted straight and parallel on the PCB so that the components can be inserted later.%

Without assistive tools, this is a pretty fiddly task. The simplest solution to this problem is to plug the pin sockets onto the corresponding components and solder them to the PCB. This ensures that the components fit exactly later.%

\subsection{TO-220 \& A4988 Cooling}%
The Open3DScanner does not use active cooling, but it is recommended to cool some parts passively.%

On the one hand the \hrefIdx{https://www.pololu.com/product/1182}{A4988 Stepper Drivers} should be equipped with a heat sink. If the stepper drivers get too warm, you may experience strange behavior (like missed steps). This is especially true if the stepper drivers are set to above \SI{1}{\ampere}.%

Furthermore, there are two \hrefIdx{https://www.centralsemi.com/PDFS/CASE/TO\_220\_PD.PDF}{TO-220} components on the board: the \hrefIdx{https://www.infineon.com/cms/en/product/power/mosfet/12v-300v-n-channel-power-mosfet/irlb8721/}{IRLB 8721} and the \hrefIdx{https://www.analog.com/en/products/lt1086.html}{LT1086CT-5}. The \hrefIdx{https://www.analog.com/en/products/lt1086.html}{LT1086CT-5} generates a lot of heat during operation, which can shorten the lifetime of the component considerably. For this reason I strongly recommend the use of thermal paste and a suitable heat sink.%

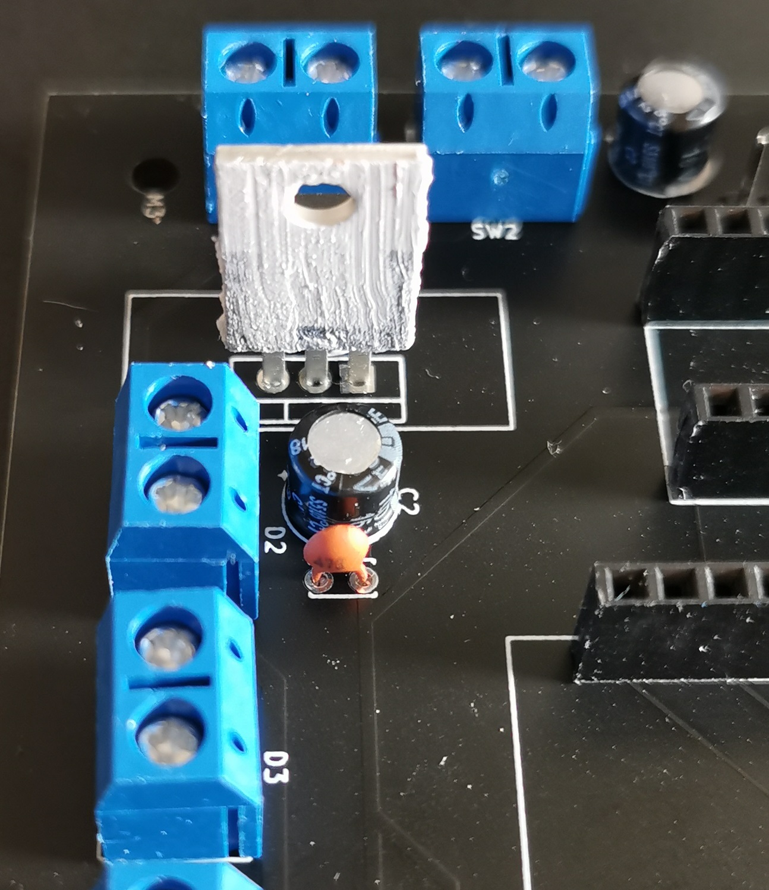
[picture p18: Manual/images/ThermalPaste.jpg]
\marginElement{\captionof{figure}{Apply a thin layer of thermal paste\dots}}%
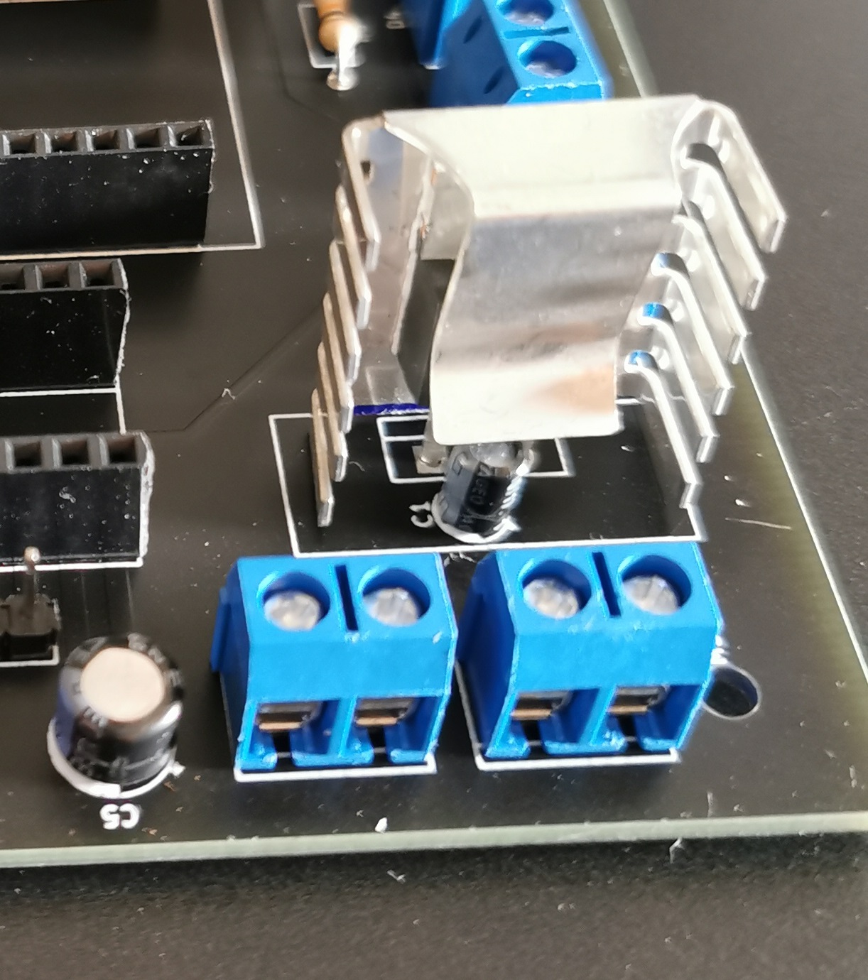
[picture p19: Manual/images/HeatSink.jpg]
\marginElement{\captionof{figure}{\dots before installing the heat sink}}%

For the \hrefIdx{https://www.infineon.com/cms/en/product/power/mosfet/12v-300v-n-channel-power-mosfet/irlb8721/}{IRLB 8721} I didn't check to what extent it generates heat during operation, but according to the principle "better safe than sorry" I recommend the use of heat conducting paste and heat sink.%

Make sure that the heat sinks do not touch any other components or the circuit board. Especially with the \hrefIdx{https://www.analog.com/en/products/lt1086.html}{LT1086CT-5} it is a bit tight, because a high packing density is needed for an optimal function of the component.%

If you are using the TO-220 heat sinks I specified in the BOM, please note the following: Depending on how deep the pins are inserted into the PCB before soldering, it may be necessary to remove the bottom fin from the heat sink. Otherwise the heat sinks do not fit on the PCB, because they cannot put pressure on the component, which is necessary with the attachable heat sinks.%

\subsection{Prepare the LED Strip}%
The instructions in this section must be repeated for each light that will be connected to the Open3DScanner. While it is possible to operate the Open3DScanner with up to four lights simultaneously, I only use two.%

For the construction of the lights it is first necessary to prepare the LED strip. The LED strip is marked at regular intervals. At these markings it is possible to divide the strip.%

For the lights of the Open3DScanner \SI{15}{\centi\meter} long strips are needed. This corresponds to three segments of three LEDs. Figure~\ref{fig:ledStrip} shows such a \SI{15}{\centi\meter} piece of LED strip.%

\begin{figure}[ht!]%
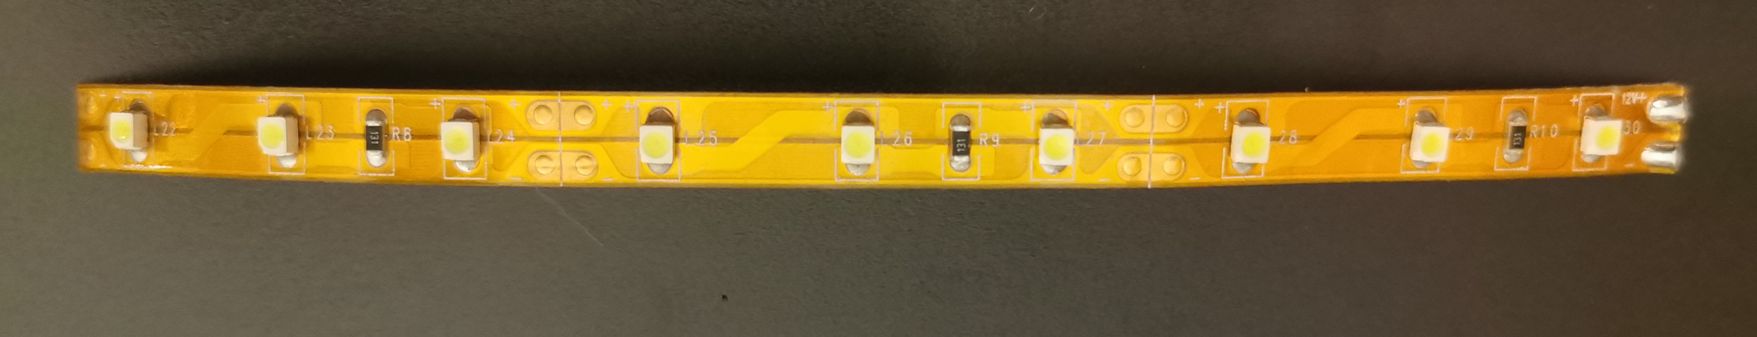
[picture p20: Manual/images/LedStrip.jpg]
	%
	\caption{One piece of LED strip as used in the Open3DScanner}%
	\label{fig:ledStrip}%
\end{figure}%

Each light of the Open3DScanner uses eight of these short strips and thus 72 LEDs.%

\begin{figure}[ht!]%
	\begin{centered}%
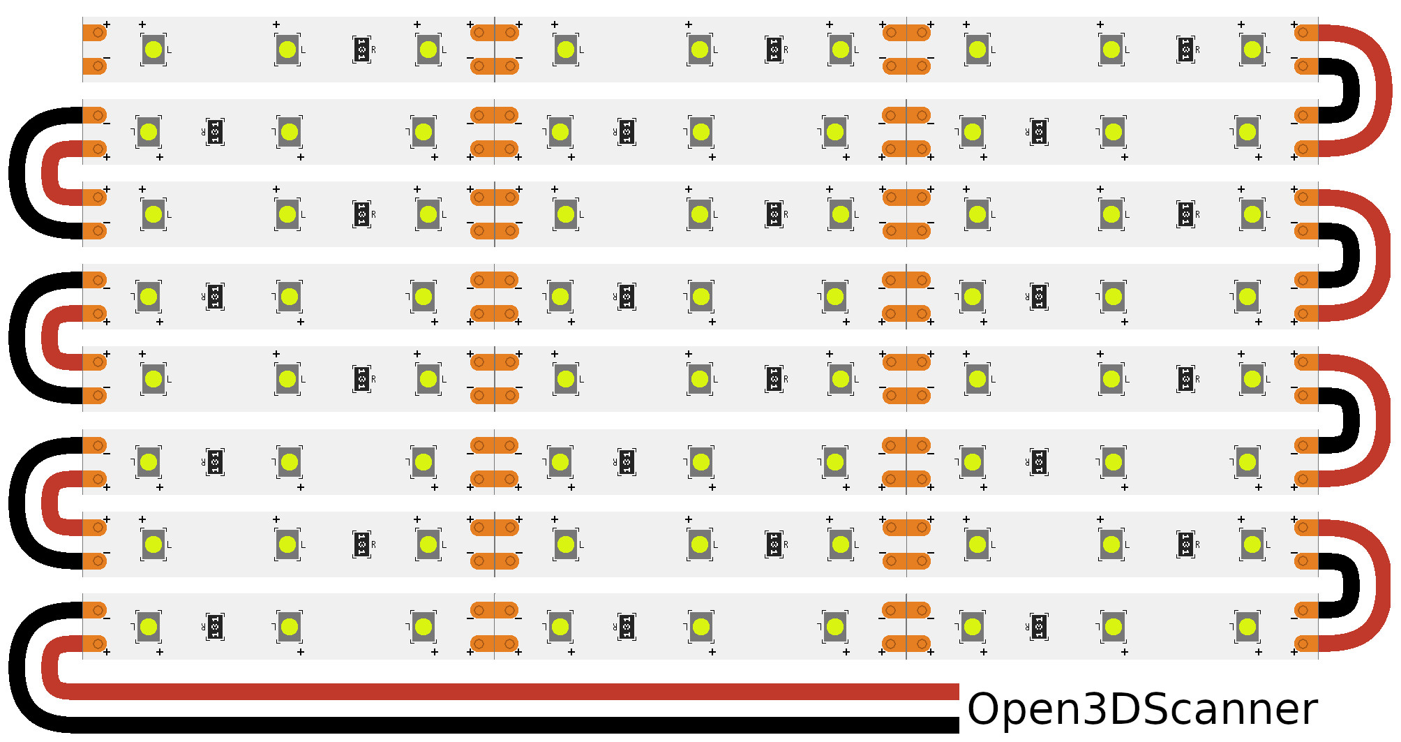
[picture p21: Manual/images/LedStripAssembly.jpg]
		%
		\caption{Schematic representation of the soldered LED strip for one light}%
		\label{fig:ledStripAssembly}%
	\end{centered}%
\end{figure}%

After dividing the LED Strip we need seven about \SI{7}{\centi\meter} long pieces of \SI{0.75}{\milli\meter\squared} cable with two wires each (for + and -). These are used to connect the segments of the LED strip to each other. We also need a approx. \SI{60}{\centi\meter} cable, which is used for the connection to the Open3DScanner. This cable can be shortened as soon as the lights are mounted and the cable is properly laid.%

Now the individual pieces of the LED strip are soldered together in series and the long cable is soldered to one end.%

It is important that no Molex connector is attached to the long cable at this point, otherwise we will not be able to lay the cable as intended. In general, it makes sense to attach the connector after the cable has been shortened to the correct length.%

A schematic representation of how the result of the soldering should look like can be found in figure~\ref{fig:ledStripAssembly}. When soldering, be sure to connect the right contacts.%

Now the soldered LED strip is glued to the Spotlight-Frame. One strip is glued in the middle of each of the recesses. Make sure that the long cable is at the lower end.%

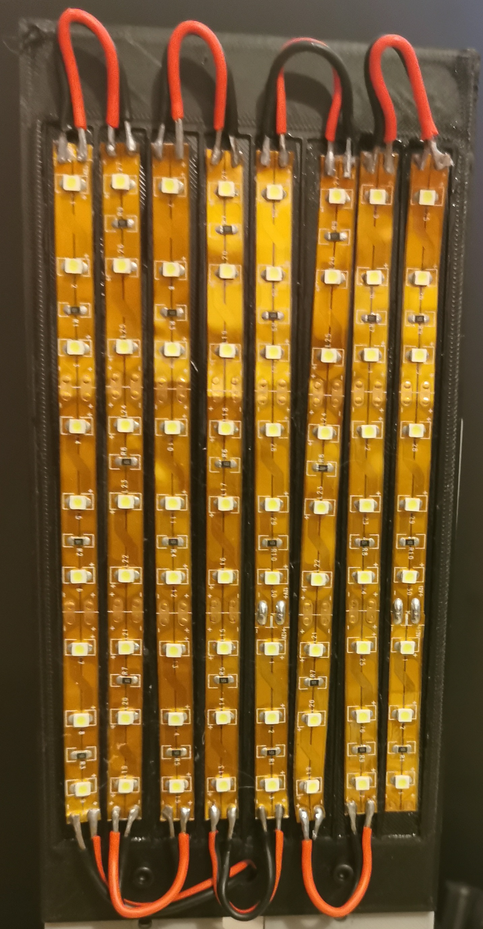
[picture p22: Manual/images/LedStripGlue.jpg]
\marginElement{\captionof{figure}{Soldered LED strip glued into printed part}\label{fig:ledStripGlue}}%

The end of the long cable is led through the hole, which is in the lower area, in the middle of the part. Figure~\ref{fig:ledStripGlue} shows what the result should look like.%

The LED strip is glued in with the pre-assembled M3 adhesive tape. If this is not strong enough and the LED strips come loose again, you can simply spread some liquid glue on the printed part and then press the LED strip in again.

The LED strip is now ready for the assembly of the light which is described in section~\ref{sec:assembly}.

\subsection{Preparing the Cables}
In this section the cables used in the Open3DScanner are described in more detail. This is explicitly not a manual for crimping, there are very good sources for this\sideNote{There are many good instructions for crimping various connections on the Internet. For example, for crimping \hrefIdx{https://www.instructables.com/id/Dupont-Crimp-Tool-Tutorial/}{Dupont cables}, \hrefIdx{https://www.molex.com/molex/common/staticLoader.jsp?fileName=/tnotes/crimp.html\&progLink=Good+Crimps\&\&channel=...Micro-Fit\&channelId=0}{Molex Micro Fit}, and \hrefIdx{https://www.klauke.com/en/electrical/sectors-solutions/technical-reports/crimping-cable-lugs-correctly/}{cable lugs}. {\faYoutube} \hrefIdx{https://www.youtube.com/results?search\_query=crimping+tutorial}{YouTube} is a great source for tutorials, too.}.%

Instead, the following paragraphs describe the individual cables and their connections.%

A schematic diagram is given for each cable, which clearly shows how cables are aligned, if necessary.%

Power cables are shown in red (+) and black (GND), while all data cables are shown in blue. This colour coding is reused in later illustrations and thus simplifies orientation.%

The cable lengths specified do not include the length of the connectors which are used for each cable.%

\paragraph{LED Strip}\mbox{}\\%

\sideTabularx[LED strip cable characteristics]{%
	\rowcolors{2}{tableLineTwo}{tableLineOne}% specify rowcolors in tabularx style
	\begin{tabularx} {\marginparwidth} {>{\rowmac \hsize=\hsize}X>{\rowmac \hsize=\hsize}X<{\clearrow}}%
		\tabularxHeader%
		Characteristic & Value\\%
		Quantity & 4\\%
		Wire Gauge & \SI{0.75}{\milli\meter\squared}\\%
		Length & \SI{15}{\centi\meter}\\%
		End A Connector & Ferrule Crimp\\%
		End B Connector & Micro-Fit - 1x2-pin, male\\%
		End A connects & PCB contacts D2, D3, D4, D5\\%
		End B connects & Open3DScanner housing\\%
	\end{tabularx}%
}%

%
{\captionof{figure}{Schematic representation of the LED strip cable}}% Take note of the surrounding {} to encapsulate special format settings

During assembly, the Molex connectors are clamped into the housing of the Open3DScanner so that they are directly accessible from the outside and the lights can be connected with a suitable Molex plug.%

Since ferrule crimps are necessary for the \SI{0.75}{\milli\meter\squared} cables, they may sit very tight in the screw terminals afterwards, which is no problem.%

Even if no or less than four lights will be connected to the Open3DScanner, it is necessary to prepare four of these cables so that there will be no gaps in the case later.%

The corresponding female connectors need to be added to the LED strips. This cable is not shown here. Just ensure that the polarity matches these cables.%

\clearpage%

\paragraph{Power Cables}\mbox{}\\%

\sideTabularx[Power connection cable characteristics]{%
	\rowcolors{2}{tableLineTwo}{tableLineOne}% specify rowcolors in tabularx style
	\begin{tabularx} {\marginparwidth} {>{\rowmac \hsize=\hsize}X>{\rowmac \hsize=\hsize}X<{\clearrow}}%
		\tabularxHeader%
		Characteristic & Value\\%
		Quantity & 2\\%
		Wire Gauge & \SI{0.75}{\milli\meter\squared}\\%
		Length & \SI{16/20}{\centi\meter} (Power Jack/Rocker Switch)\\%
		End A Connector & Ferrule Crimp\\%
		End B Connector & Cable Lug\\%
		End A connects & PCB contacts J1, SW2\\%
		End B connects & Rocker Switch \& Power Jack\\%
	\end{tabularx}%
}%

%
{\captionof{figure}{Schematic representation of the power connection cable}}% Take note of the surrounding {} to encapsulate special format settings

Two identical cables are used to connect the power source to the PCB and to connect the rocker switch, which allows the device to be switched on and off.%

Make sure that the correct cable lugs are used for both cables. These can be different for different versions of the parts and must be selected appropriately for the components.%

\paragraph{USB Cable}\mbox{}\\%

\sideTabularx[USB cable characteristics]{%
	\rowcolors{2}{tableLineTwo}{tableLineOne}% specify rowcolors in tabularx style
	\begin{tabularx} {\marginparwidth} {>{\rowmac \hsize=\hsize}X>{\rowmac \hsize=\hsize}X<{\clearrow}}%
		\tabularxHeader%
		Characteristic & Value\\%
		Quantity & 1\\%
		Wire Gauge & Undefined\\%
		Length & \SI{15}{\centi\meter}\\%
		End A Connector & Ferrule Crimp\\%
		End B Connector & Micro USB-B\\%
		End A connects & PCB contact J2\\%
		End B connects & \hrefIdx{https://www.espressif.com/en/products/hardware/esp32-devkitc/overview}{ESP32-DevKitC}\\%
	\end{tabularx}%
}%

%
{\captionof{figure}{Schematic representation of the USB cable}}% Take note of the surrounding {} to encapsulate special format settings

Since an \hrefIdx{https://www.espressif.com/en/products/hardware/esp32-devkitc/overview}{ESP32-DevKitC} is used in the Open3DScanner, it is necessary to supply it with power via the Micro-USB-B socket.%

The cable diameter for the USB cable is not specified as any USB cable can be used to power the ESP32. The available USB cables on the market have different cable diameters, but it is not necessary to buy a special cable.%

\paragraph{Bi-Color LED Cable}\mbox{}\\%

\sideTabularx[Bi-color LED cable characteristics]{%
	\rowcolors{2}{tableLineTwo}{tableLineOne}% specify rowcolors in tabularx style
	\begin{tabularx} {\marginparwidth} {>{\rowmac \hsize=\hsize}X>{\rowmac \hsize=\hsize}X<{\clearrow}}%
		\tabularxHeader%
		Characteristic & Value\\%
		Quantity & 1\\%
		Wire Gauge & \SI{0.2}{\milli\meter\squared}\\%
		Length & \SI{11}{\centi\meter}\\%
		End A Connector & 3-Pin Dupont\\%
		End B Connector & 3-Pin Dupont\\%
		End A connects & PCB contact D1\\%
		End B connects & Bi-color LED\\%
	\end{tabularx}%
}%

%
{\captionof{figure}{Schematic representation of the bi-color LED cable}}% Take note of the surrounding {} to encapsulate special format settings

The bi-color LED is plugged directly into the Dupont connector.%

When assembling this cable it is important to pay attention to the cable assignment. The two plugs are not connected identically.%

\clearpage%

\paragraph{Encoder Cable}\mbox{}\\%

\sideTabularx[Encoder cable characteristics]{%
	\rowcolors{2}{tableLineTwo}{tableLineOne}% specify rowcolors in tabularx style
	\begin{tabularx} {\marginparwidth} {>{\rowmac \hsize=\hsize}X>{\rowmac \hsize=\hsize}X<{\clearrow}}%
		\tabularxHeader%
		Characteristic & Value\\%
		Quantity & 1\\%
		Wire Gauge & \SI{0.2}{\milli\meter\squared}\\%
		Length & \SI{15}{\centi\meter}\\%
		End A Connector & 3-Pin Dupont\\%
		End B Connector & 2$\times$3-Pin Dupont\\%
		End A connects & PCB contact SW1\\%
		End B connects & Rotary Encoder\\%
	\end{tabularx}%
}%

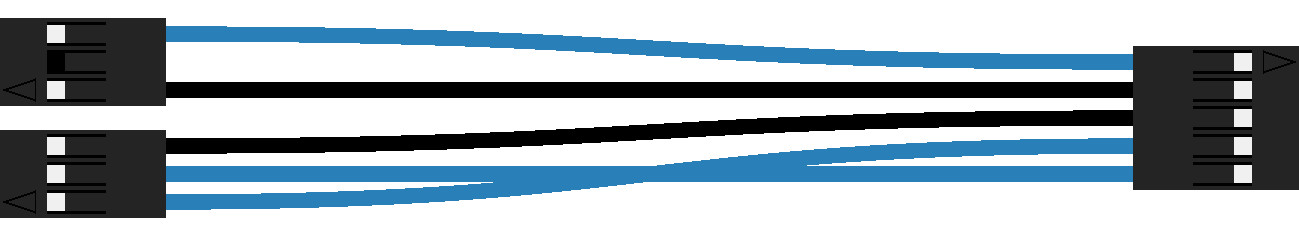
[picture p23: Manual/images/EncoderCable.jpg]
%
{\captionof{figure}{Schematic representation of the encoder cable}}% Take note of the surrounding {} to encapsulate special format settings

As with the bi-color LED, the cable for the encoder is connected directly to the component. However, there is a special aspect here which is given by the pin layout of the encoder used.%

The pins of the encoder are arranged in two rows (2 + 3). The pins of the 2-series are arranged like a 3-series, where the middle pin is missing. For this reason, two 3-pin Dupont housings are used on the component side, where one space remains unoccupied.%

\paragraph{Display Cable}\mbox{}\\%

\sideTabularx[Display cable characteristics]{%
	\rowcolors{2}{tableLineTwo}{tableLineOne}% specify rowcolors in tabularx style
	\begin{tabularx} {\marginparwidth} {>{\rowmac \hsize=\hsize}X>{\rowmac \hsize=\hsize}X<{\clearrow}}%
		\tabularxHeader%
		Characteristic & Value\\%
		Quantity & 1\\%
		Wire Gauge & \SI{0.2}{\milli\meter\squared}\\%
		Length & \SI{15}{\centi\meter}\\%
		End A Connector & 8-Pin Dupont\\%
		End B Connector & 8-Pin Dupont\\%
		End A connects & PCB contact DS1\\%
		End B connects & Display\\%
	\end{tabularx}%
}%

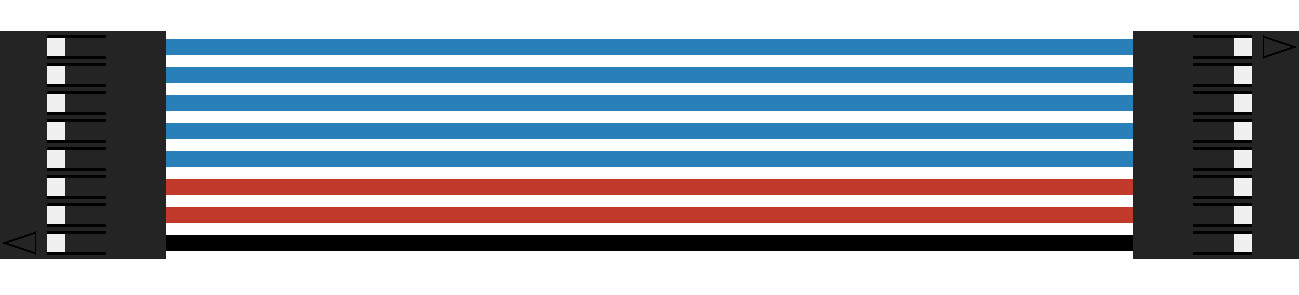
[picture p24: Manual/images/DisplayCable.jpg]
%
{\captionof{figure}{Schematic representation of the display cable}}% Take note of the surrounding {} to encapsulate special format settings

Since the used display is mounted on a printed circuit board, the cable is connected to the two pin headers on the display and the PCB.

\section{Assembly the Open3DScanner}%
\label{sec:assembly}
After all the necessary preparatory work has been done, the actual instructions for building the Open3DScanner follow.%

Each individual step is illustrated by an figure. In addition, each step is provided with a short instruction and, if useful, further tips, warnings and notes are given.%

At each step all used components are listed. If these partially assembled parts are subsequently used in further steps, they will not be listed again.%

At the end there are further illustrations, which contain exact dimensions and orientations of parts.%
\clearpage%

% STEP 1
\sideTabularx[Required parts for step 1]{%
	\rowcolors{2}{tableLineTwo}{tableLineOne}% specify rowcolors in tabularx style
	\begin{tabularx} {\marginparwidth} {>{\rowmac \hsize=1.5\hsize}X>{\rowmac \hsize=0.5\hsize}X<{\clearrow}}%
		\tabularxHeader%
		Part & Quantity\\%
		Rotor-Stand & 1\\%
		Passive-Stand & 1\\%
		625ZZ Bearing & 2\\%
	\end{tabularx}%
}%

\marginInfo*[Instructions]{Press one bearing into each of the openings provided in the upper area of the printed parts. The bearings should be flush with the surface of the printed parts.}%

\marginTips*[Tip]{If the opening for the bearings is a tad too tight, you can use pliers to press the bearings into the opening. In this case a piece of fabric or tissue should be placed between the pliers and the components to avoid craters and deformation.}%

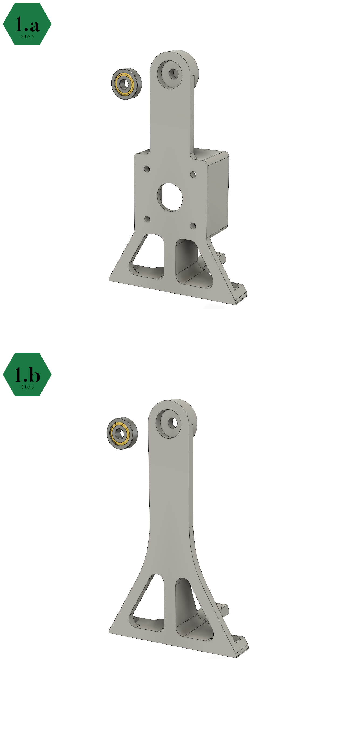
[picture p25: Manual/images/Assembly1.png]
%
{\captionof{figure}{Step 1 of the Open3DScanner assembly}}
\clearpage%

% STEP 2&3
\sideTabularx[Required parts for step 2]{%
	\rowcolors{2}{tableLineTwo}{tableLineOne}% specify rowcolors in tabularx style
	\begin{tabularx} {\marginparwidth} {>{\rowmac \hsize=1.5\hsize}X>{\rowmac \hsize=0.5\hsize}X<{\clearrow}}%
		\tabularxHeader%
		Part & Quantity\\%
		Nema 17 Stepper Motor & 2\\%
		Nema 17 Damper & 2\\%
		M3$\times$6 & 4\\%
	\end{tabularx}%
}%

\marginInfo*[Instructions]{Screw the dampers to the stepper motors.}%

\marginTips*[Tip]{The orientation of the dampers does not matter, it is only important that the side with the threads points away from the stepper motor.}%

\sideTabularx[Required parts for step 3]{%
	\vspace{2.65cm}%
	\rowcolors{2}{tableLineTwo}{tableLineOne}% specify rowcolors in tabularx style
	\begin{tabularx} {\marginparwidth} {>{\rowmac \hsize=1.5\hsize}X>{\rowmac \hsize=0.5\hsize}X<{\clearrow}}%
		\tabularxHeader%
		Part & Quantity\\%
		M3$\times$8 & 2\\%
	\end{tabularx}%
}%

\marginInfo*[Instructions]{Screw one stepper motor to the Rotor-Stand.}%

\marginCheck*[Check]{Make sure that the cables are pointing downwards to simplify the wiring later on.}%

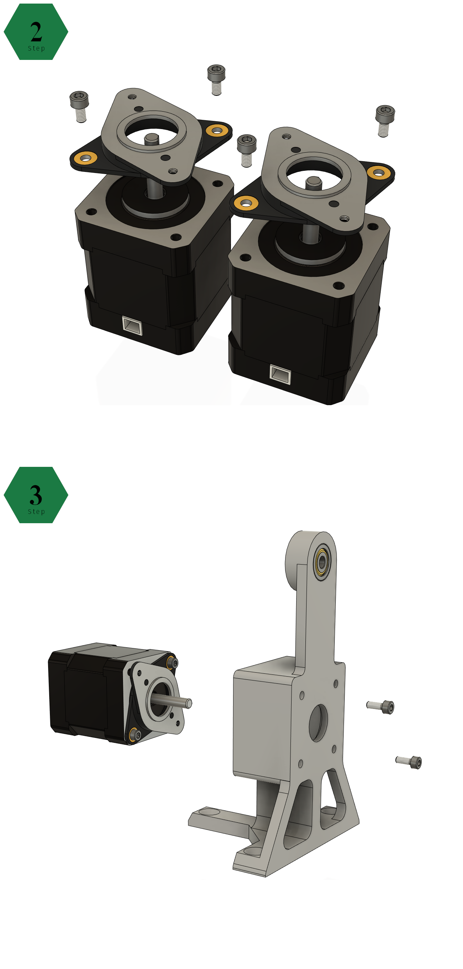
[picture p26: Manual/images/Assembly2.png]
%
{\captionof{figure}{Step 2 \& 3 of the Open3DScanner assembly}}
\clearpage%

% STEP 4
\sideTabularx[Required parts for step 4]{%
	\rowcolors{2}{tableLineTwo}{tableLineOne}% specify rowcolors in tabularx style
	\begin{tabularx} {\marginparwidth} {>{\rowmac \hsize=1.5\hsize}X>{\rowmac \hsize=0.5\hsize}X<{\clearrow}}%
		\tabularxHeader%
		Part & Quantity\\%
		Rotor-Gear & 1\\%
		Rotor-Pinion & 1\\%
		\SI{5}{\milli\meter} $\times$ \SI{26}{\milli\meter} Steel Rod & 1\\%
	\end{tabularx}%
}%

\marginInfo*[Instructions]{Press the Rotor-Pinion onto the shaft of the stepper motor. Press the steel rod into the bearing so that it is countersunk as far as possible in the printed part without hindering free rotation. Push the Rotor-Gear onto the steel rod. Use the middle hole of the Rotor-Gear for this.}%

\marginTips*[Tip]{The Rotor-Gear and the steel rod will not be flush. This is not problematic and improves the stability of the assembly in later steps.}%

\marginWarning*[Double check]{The design does not ensure alignment between the two gears. It is intended that the rotor gear is centered on the rotor pinion and protrudes about 1mm on both sides. This must be strictly adhered to in order to allow a smooth movement later on. The connections are so tight that the parts should not slip after alignment.}%

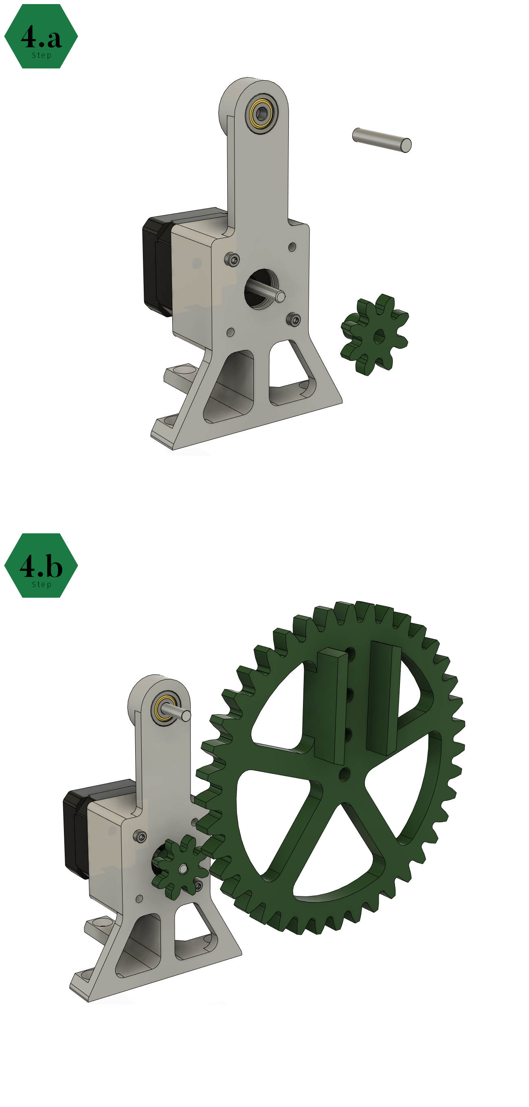
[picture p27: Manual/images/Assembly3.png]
%
{\captionof{figure}{Step 4 of the Open3DScanner assembly}}
\clearpage%

% STEP 5
\sideTabularx[Required parts for step 5]{%
	\rowcolors{2}{tableLineTwo}{tableLineOne}% specify rowcolors in tabularx style
	\begin{tabularx} {\marginparwidth} {>{\rowmac \hsize=1.5\hsize}X>{\rowmac \hsize=0.5\hsize}X<{\clearrow}}%
		\tabularxHeader%
		Part & Quantity\\%
		Rotor-Arm & 2\\%
		Turntable-Arm & 1\\%
		\SI{5}{\milli\meter} $\times$ \SI{26}{\milli\meter} Steel Rod & 2\\%
	\end{tabularx}%
}%

\marginInfo*[Instructions]{Press one Rotor-Arm on each end of the Turntable-Arm so that they are flush with the holes. Press a steel rod into each of the holes to firmly join the components together. The steel rods should be flush with the Rotor-Arm on both sides.}%

\marginCheck*[Check]{Make sure that the Turntable-Arm is correctly turned to prevent subsequent disassembly and correction.}%

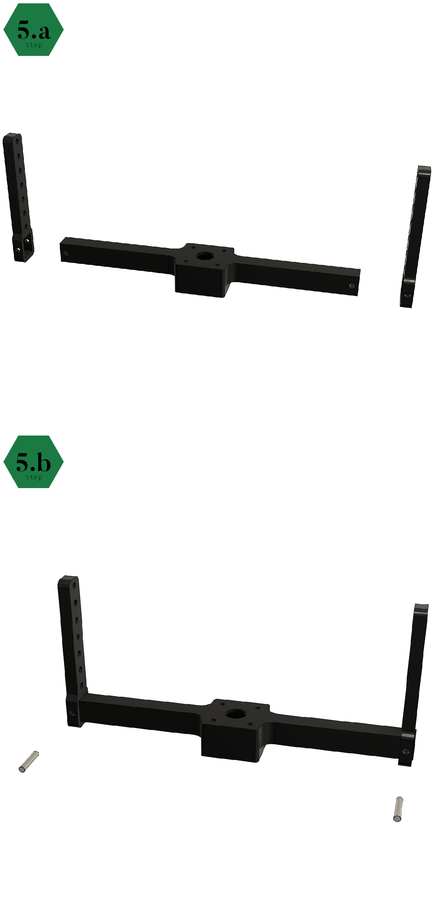
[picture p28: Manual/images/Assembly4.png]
%
{\captionof{figure}{Step 5 of the Open3DScanner assembly}}
\clearpage%

% STEP 6 & 7
\sideTabularx[Required parts for step 6]{%
	\rowcolors{2}{tableLineTwo}{tableLineOne}% specify rowcolors in tabularx style
	\begin{tabularx} {\marginparwidth} {>{\rowmac \hsize=1.5\hsize}X>{\rowmac \hsize=0.5\hsize}X<{\clearrow}}%
		\tabularxHeader%
		Part & Quantity\\%
		M3$\times$8 & 2\\%
	\end{tabularx}%
}%

\marginInfo*[Instructions]{Screw the remaining stepper motor to the Turntable-Arm.}%

\sideTabularx[Required parts for step 7]{%
	\vspace{5.7cm}%
	\rowcolors{2}{tableLineTwo}{tableLineOne}% specify rowcolors in tabularx style
	\begin{tabularx} {\marginparwidth} {>{\rowmac \hsize=1.5\hsize}X>{\rowmac \hsize=0.5\hsize}X<{\clearrow}}%
		\tabularxHeader%
		Part & Quantity\\%
		\SI{5}{\milli\meter} $\times$ \SI{26}{\milli\meter} Steel Rod & 1\\%
	\end{tabularx}%
}%

\marginInfo*[Instructions]{Push the steel rod through the upper hole of one Rotor-Arm and then into the outer hole of the Rotor-Gear. The components should be flush with each other and the Rotor-Arm is fixed to the rotor gear by the two jaws.}%

\marginQuestion*[Information]{The Rotor-Arm is additionally fixed by the steel rod, which connects the Rotor-Gear with the Rotor-Stand.}%

\marginCheck*[Check]{Make sure that the motor cables point towards you when the Rotor-Stand is on the left side. This will allow clean wiring.}%

\marginCritical*[Warning]{For accurate alignment of the steel bar, consider the image cutout. The rod must protrude a little bit from the rotor arm, otherwise the rotation of the device will be blocked.}%

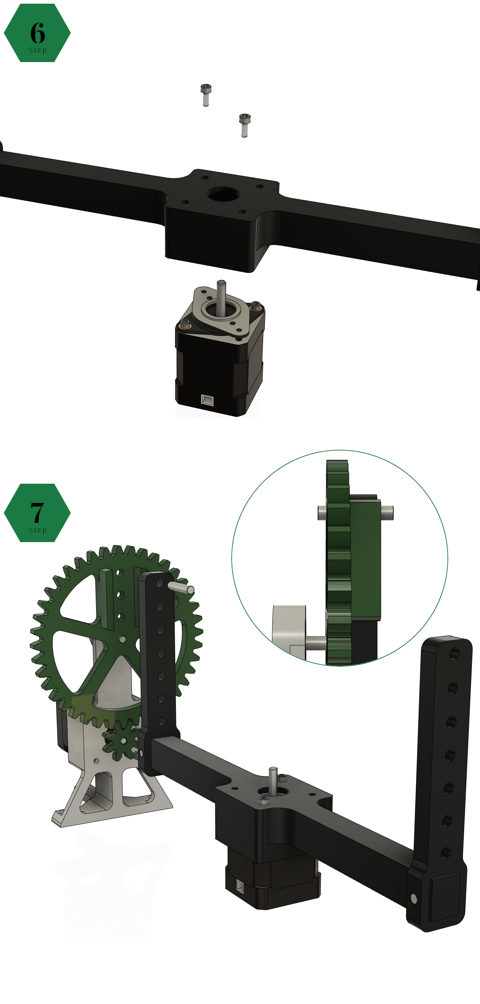
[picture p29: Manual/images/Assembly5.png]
%
{\captionof{figure}{Step 6 \& 7 of the Open3DScanner assembly}}
\clearpage%

% STEP 8 & 9
\sideTabularx[Required parts for step 8]{%
	\rowcolors{2}{tableLineTwo}{tableLineOne}% specify rowcolors in tabularx style
	\begin{tabularx} {\marginparwidth} {>{\rowmac \hsize=1.5\hsize}X>{\rowmac \hsize=0.5\hsize}X<{\clearrow}}%
		\tabularxHeader%
		Part & Quantity\\%
		\SI{5}{\milli\meter} $\times$ \SI{26}{\milli\meter} Steel Rod & 1\\%
	\end{tabularx}%
}%

\marginInfo*[Instructions]{Connect the other Rotor-Arm to the bearing in the Passive-Stand. Use the center hole in the Rotor-Arm for this. The rod will be flush with the Rotor-Arm and protrude a bit from the back of the Passive-Stand.}%

\sideTabularx[Required parts for step 9]{%
	\vspace{5.0cm}%
	\rowcolors{2}{tableLineTwo}{tableLineOne}% specify rowcolors in tabularx style
	\begin{tabularx} {\marginparwidth} {>{\rowmac \hsize=1.5\hsize}X>{\rowmac \hsize=0.5\hsize}X<{\clearrow}}%
		\tabularxHeader%
		Part & Quantity\\%
		Turntable-Medium & 1\\%
	\end{tabularx}%
}%

\marginInfo*[Instructions]{Push the Turntable-Medium as far as possible onto the shaft of the stepper motor, which is mounted to the Turntable-Arm.}%

\marginTips*[Tip]{Stabilize the structure by pressing against the bottom of the Turntable-Arm while pushing the Turntable-Medium onto the motor shaft. That way bending and deformation of the parts can be prevented.}%

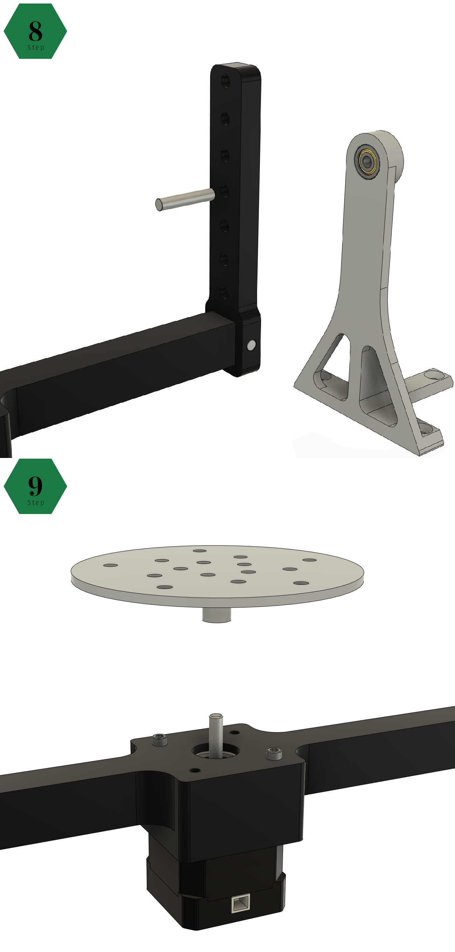
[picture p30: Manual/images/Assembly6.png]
%
{\captionof{figure}{Step 8 \& 9 of the Open3DScanner assembly}}
\clearpage%

% STEP 10
\sideTabularx[Required parts for step 10]{%
	\rowcolors{2}{tableLineTwo}{tableLineOne}% specify rowcolors in tabularx style
	\begin{tabularx} {\marginparwidth} {>{\rowmac \hsize=1.5\hsize}X>{\rowmac \hsize=0.5\hsize}X<{\clearrow}}%
		\tabularxHeader%
		Part & Quantity\\%
		Spotlight-Stand & 1\\%
		Spotlight-Frame & 1\\%
		M3$\times$8 & 2\\%
		M3 Nut & 2\\%
	\end{tabularx}%
}%

\marginInfo*[Instructions]{Press the two nuts into the recesses of the Spotlight-Stand. Select two adjacent holes that are at the same height. Next attach the Spotlight-Frame with the Spotlight-Stand. To do this, screw the screws through the holes in the Spotlight-Frame with the nuts on the back of the Spotlight-Stand.}%

\marginTips*[Tip]{Repeat this step up to four times for each spotlight you want to use. The height of the Spotlight frame can be changed by inserting the nuts into other recesses. This allows the illumination for the scans to be changed. The hole in the middle of the lower part of the Spotlight-Frame is for cable routing.}%

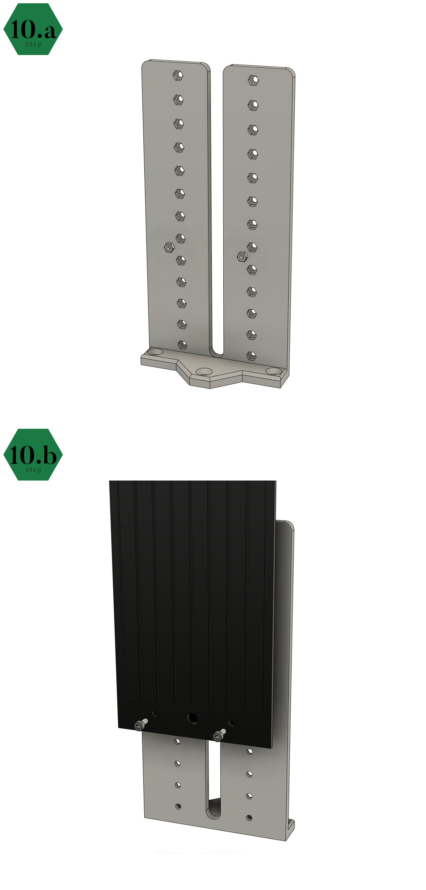
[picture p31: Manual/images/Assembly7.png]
%
{\captionof{figure}{Step 10 of the Open3DScanner assembly}}
\clearpage%

% STEP 11
\sideTabularx[Required parts for step 11]{%
	\rowcolors{2}{tableLineTwo}{tableLineOne}% specify rowcolors in tabularx style
	\begin{tabularx} {\marginparwidth} {>{\rowmac \hsize=1.5\hsize}X>{\rowmac \hsize=0.5\hsize}X<{\clearrow}}%
		\tabularxHeader%
		Part & Quantity\\%
		Foot-Holder-Clamp & 4\\%
		\SI{30}{\milli\meter} $\times$ \SI{15}{\milli\meter} Rubber Feet & 4\\%
		M3$\times$20 & 4\\%
		M3 Nut & 4\\%
	\end{tabularx}%
}%

\marginInfo*[Instructions]{Press the nut into the recess on top of the Foot-Holder-Clamp. Then screw the rubber feet with the screw from the bottom to the nut.}%

\marginTips*[Tip]{Repeat this step four times to assemble all feet for the base plate.}%

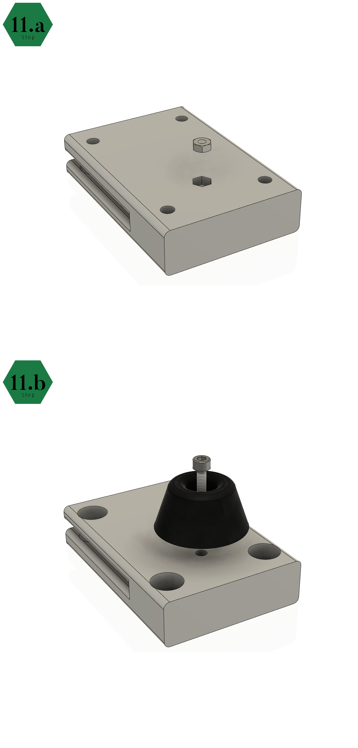
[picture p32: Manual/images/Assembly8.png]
%
{\captionof{figure}{Step 11 of the Open3DScanner assembly}}
\clearpage%

% STEP 12
\sideTabularx[Required parts for step 12]{%
	\rowcolors{2}{tableLineTwo}{tableLineOne}% specify rowcolors in tabularx style
	\begin{tabularx} {\marginparwidth} {>{\rowmac \hsize=1.5\hsize}X>{\rowmac \hsize=0.5\hsize}X<{\clearrow}}%
		\tabularxHeader%
		Part & Quantity\\%
		\SI{400}{\milli\meter} $\times$ \SI{550}{\milli\meter} $\times$ \SI{16}{\milli\meter} Wooden Board & 1\\%
		Backplate-Holder & 2\\%
		4.0$\times$16 Countersunk Wood Screwt & 24\\%
	\end{tabularx}%
}%

\marginInfo*[Instructions]{Screw the parts to the wooden board which is used as base plate. Use four screws for each assembled foot and Backplate-Holder. On the underside of the wooden board, mount one foot flush in each corner. The horizontal opening points into the inner area of the plate. The openings of two feet, which are mounted along the long edge of the base plate, face each other. The backplate holders are mounted from the top of the base plate. They are mounted flush in the corners of one of the long edges of the wooden board. The Backplate-Holder inserts have to be parallel to the long edge of the base plate.}%

\marginTips*[Tip]{For scans the backplate is inserted into the Backplate-Holders. When the scanner should be stored the backplate can be slided into the Foot-holder-Clamps to reduce the volume of the scanner.}%

\marginCheck*[Check]{You need to mount four assembled feets and two Backplate-Holder.}%

\marginCritical*[Warning]{Align the components as well as possible at the corners of the wooden board. Otherwise it can happen that the rear panel does not fit properly or that parts cannot be screwed down because the screws on the top and bottom side collide.}%

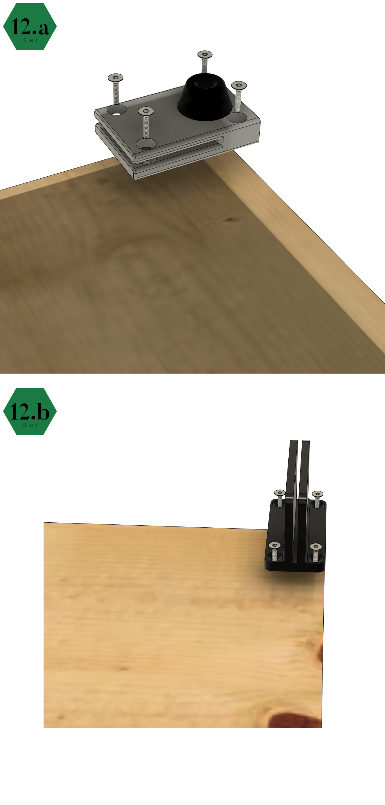
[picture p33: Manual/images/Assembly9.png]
%
{\captionof{figure}{Step 12 of the Open3DScanner assembly}}
\clearpage%

% STEP 13
\sideTabularx[Required parts for step 13]{%
	\rowcolors{2}{tableLineTwo}{tableLineOne}% specify rowcolors in tabularx style
	\begin{tabularx} {\marginparwidth} {>{\rowmac \hsize=1.5\hsize}X>{\rowmac \hsize=0.5\hsize}X<{\clearrow}}%
		\tabularxHeader%
		Part & Quantity\\%
		Housing-Main & 1\\%
		\SI{5.5}{\milli\meter}$\times$\SI{2.1}{\milli\meter} Female DC Power Jack Panel Mount (L722AS) & 1\\%
		\SI{5/8}{''} Rubber Seal Ring & 1\\%
	\end{tabularx}%
}%

\marginInfo*[Instructions]{Press the rubber seal into the opening provided in the back of the housing. Mount the power jack in the opening on the left side of the case.}%

\marginTips*[Tip]{If your power jack does not have the accessories for mounting, you will need a M8 nut and a \SI{1}{\milli\meter} washer with \SI{8}{\milli\meter} diameter in addition. Pliers simplify the tightening of the nut. In order to simplify the wiring, it makes sense to attach the power cable to the jack first.}%

\marginCritical*[Warning]{Make sure that the power jack is aligned as shown in the illustration, otherwise the PCB may not fit into the case anymore.}%

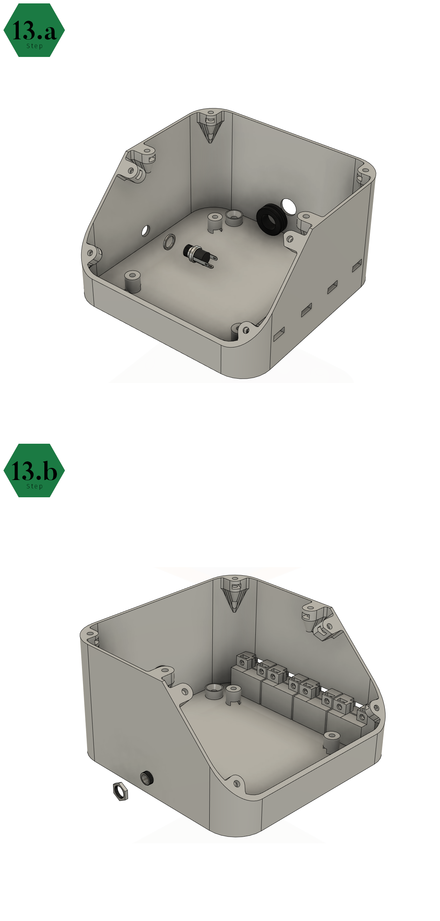
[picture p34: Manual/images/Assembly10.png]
%
{\captionof{figure}{Step 13 of the Open3DScanner assembly}}
\clearpage%

% STEP 14
\sideTabularx[Required parts for step 14]{%
	\rowcolors{2}{tableLineTwo}{tableLineOne}% specify rowcolors in tabularx style
	\begin{tabularx} {\marginparwidth} {>{\rowmac \hsize=1.5\hsize}X>{\rowmac \hsize=0.5\hsize}X<{\clearrow}}%
		\tabularxHeader%
		Part & Quantity\\%
		Molex crimp housing --- Micro-Fit - 1x2-pin, male (430200201) & 4\\%
		M3 Nut & 8\\%
	\end{tabularx}%
}%

\marginInfo*[Instructions]{Mount the Micro-Fit connectors. Make sure that the mounting hook points to the rear of the housing. The connectors are first pressed against the housing wall and pushed into the recess. Then they are pushed out a little bit so that they are flush with the outside of the housing. Slide the nuts into the openings.  Two nuts are required for each connector.}%

\marginTips*[Tip]{Before mounting the Micro-Fit connectors, connect the cables to them.}%

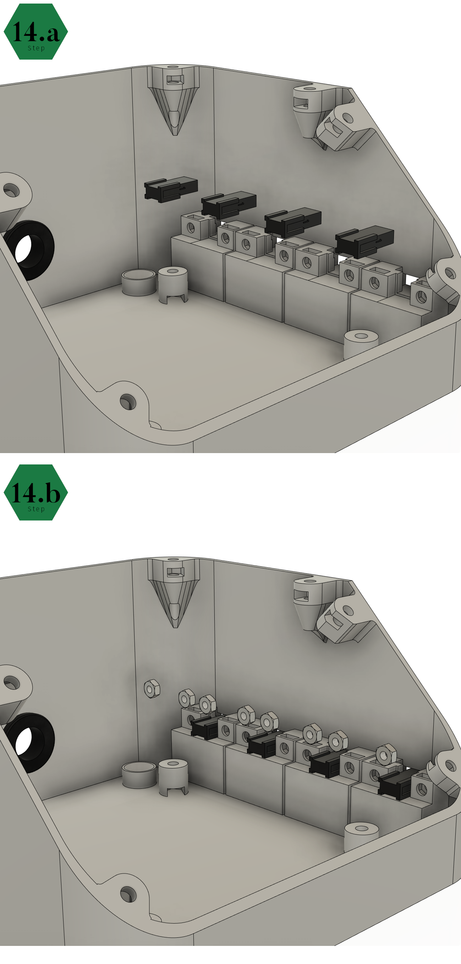
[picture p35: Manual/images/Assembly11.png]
%
{\captionof{figure}{Step 14 of the Open3DScanner assembly}}
\clearpage%

% STEP 15 & 16
\sideTabularx[Required parts for step 15]{%
	\rowcolors{2}{tableLineTwo}{tableLineOne}% specify rowcolors in tabularx style
	\begin{tabularx} {\marginparwidth} {>{\rowmac \hsize=1.5\hsize}X>{\rowmac \hsize=0.5\hsize}X<{\clearrow}}%
		\tabularxHeader%
		Part & Quantity\\%
		Micro-Fit-Holder-P1 & 4\\%
		Micro-Fit-Holder-P2 & 4\\%
		M3$\times$10 & 8\\%
	\end{tabularx}%
}%

\marginInfo*[Instructions]{Use one Micro-Fit-Holder-P1, one Micro-Fit-Holder-P1, and two screws to secure each Micro-Fit connectors.}%

\sideTabularx[Required parts for step 16]{%
	\vspace{4.5cm}%
	\rowcolors{2}{tableLineTwo}{tableLineOne}% specify rowcolors in tabularx style
	\begin{tabularx} {\marginparwidth} {>{\rowmac \hsize=1.5\hsize}X>{\rowmac \hsize=0.5\hsize}X<{\clearrow}}%
		\tabularxHeader%
		Part & Quantity\\%
		M3 Nut & 8\\%
	\end{tabularx}%
}%

\marginInfo*[Instructions]{Slide a nut into each opening along the top edge of the housing.}%

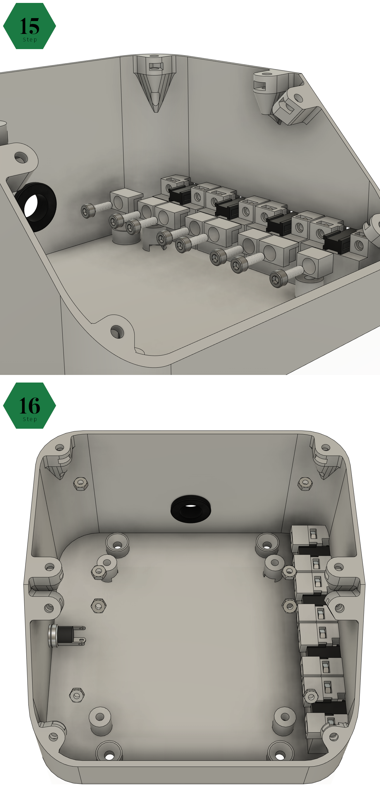
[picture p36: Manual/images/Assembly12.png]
%
{\captionof{figure}{Step 15 \& 16 of the Open3DScanner assembly}}
\clearpage%

% STEP 17
\sideTabularx[Required parts for step 17]{%
	\rowcolors{2}{tableLineTwo}{tableLineOne}% specify rowcolors in tabularx style
	\begin{tabularx} {\marginparwidth} {>{\rowmac \hsize=1.5\hsize}X>{\rowmac \hsize=0.5\hsize}X<{\clearrow}}%
		\tabularxHeader%
		Part & Quantity\\%
		PCB & 1\\%
		M3 Nut & 4\\%
		M3$\times$12 & 4\\%
	\end{tabularx}%
}%

\marginInfo*[Instructions]{Slide one nut each into the PCB stand at the bottom of the housing. Then screw the PCB into the housing.}%

\marginTips*[Tip]{The cable from the power jack can be routed below the PCB. This is much easier if it is done before the PCB is screwed down.}%

\marginCheck*[Check]{Make sure that you align the PCB as shown in the figure, otherwise the wiring may become difficult and the specified cable lengths will no longer fit.}%

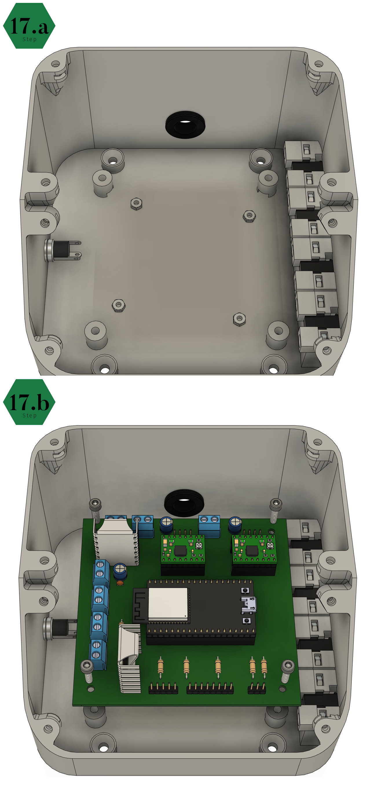
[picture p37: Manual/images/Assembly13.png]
%
{\captionof{figure}{Step 17 of the Open3DScanner assembly}}
\clearpage%

% STEP 18 & 19
\sideTabularx[Required parts for step 18]{%
	\rowcolors{2}{tableLineTwo}{tableLineOne}% specify rowcolors in tabularx style
	\begin{tabularx} {\marginparwidth} {>{\rowmac \hsize=1.5\hsize}X>{\rowmac \hsize=0.5\hsize}X<{\clearrow}}%
		\tabularxHeader%
		Part & Quantity\\%
		4.0$\times$16 Countersunk Wood Screwt & 4\\%
	\end{tabularx}%
}%

\marginInfo*[Instructions]{Screw the housing onto the wooden base plate.}%

\marginTips*[Tip]{For the exact alignment on the base plate, there is a detailed illustration at the end of the assembly instructions.}%

\sideTabularx[Required parts for step 19]{%
	\vspace{1.80cm}%
	\rowcolors{2}{tableLineTwo}{tableLineOne}% specify rowcolors in tabularx style
	\begin{tabularx} {\marginparwidth} {>{\rowmac \hsize=1.5\hsize}X>{\rowmac \hsize=0.5\hsize}X<{\clearrow}}%
		\tabularxHeader%
		Part & Quantity\\%
		STEC12E08 Rotary Encoder & 1\\%
		\SI{5}{\milli\meter} 3-Pin Bi-Color LED & 1\\%
		Nokia 5110 Display & 1\\%
		LCD-Holder & 4\\%
		LED-Holder & 1\\%
		Encoder-Holder & 1\\%
		Housing-Front & 1\\%
		M3$\times$12 & 2\\%
		M3$\times$6 & 2\\%
		M3 Nut & 8\\%
	\end{tabularx}%
}%

\marginInfo*[Instructions]{Glue the nuts for the LED and the encoder with superglue into the front panel of the housing. Press the remaining nuts into the LCD-holder. Insert the LED, encoder, and LCD into the openings provided in the front panel. Screw the LED and encoder to the front panel. Use LED-Holder and Encoder-Holder for this.}%

\marginTips*[Tip]{Depending on the manufacturer of the LCD, it may be necessary to cut a piece out of the back of the front panel, otherwise the solder points will prevent the display from sitting flush in the panel.}%

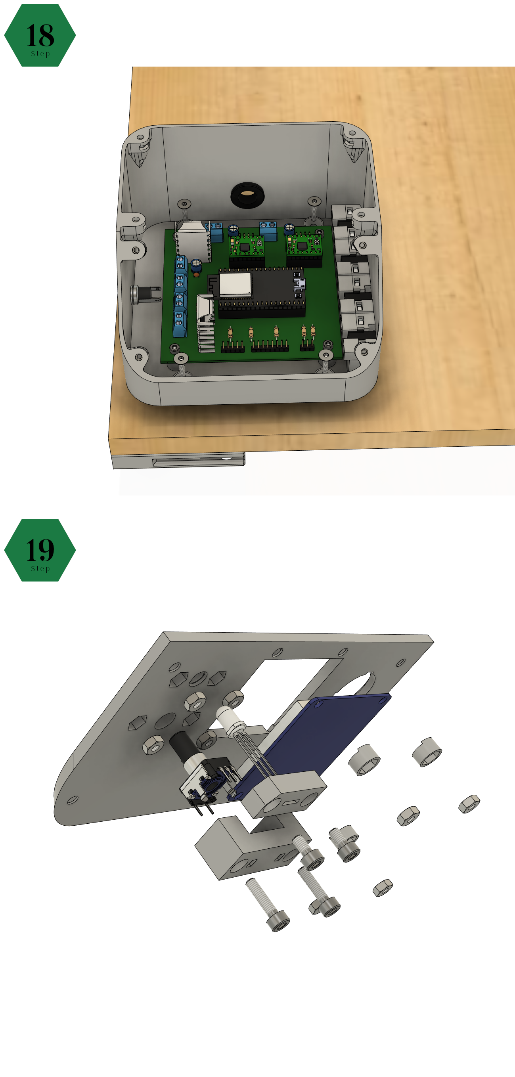
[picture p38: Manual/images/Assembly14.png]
%
{\captionof{figure}{Step 18 \& 19 of the Open3DScanner assembly}}
\clearpage%

% STEP 20 & 21
\sideTabularx[Required parts for step 20]{%
	\rowcolors{2}{tableLineTwo}{tableLineOne}% specify rowcolors in tabularx style
	\begin{tabularx} {\marginparwidth} {>{\rowmac \hsize=1.5\hsize}X>{\rowmac \hsize=0.5\hsize}X<{\clearrow}}%
		\tabularxHeader%
		Part & Quantity\\%
		Housing-Knob & 1\\%
		Round \SI{20}{\milli\meter} SPST Rocker Switch (R13 112) & 1\\%
		M3$\times$10  & 4\\%
	\end{tabularx}%
}%

\marginInfo*[Instructions]{Press the rocker switch into the recess of the front panel. Screw the display tight and pay attention to the orientation of the LCD-Holder. Press the Housing-Knob onto the shaft of the encoder.}%

\marginTips*[Tip]{Do not press the Housing-Knob too firmly on the shaft, otherwise the glued nuts will come loose.}%

\sideTabularx[Required parts for step 21]{%
	\vspace{0.80cm}%
	\rowcolors{2}{tableLineTwo}{tableLineOne}% specify rowcolors in tabularx style
	\begin{tabularx} {\marginparwidth} {>{\rowmac \hsize=1.5\hsize}X>{\rowmac \hsize=0.5\hsize}X<{\clearrow}}%
		\tabularxHeader%
		Part & Quantity\\%
		Housing-Top  & 1\\%
		M3$\times$10  & 8\\%
	\end{tabularx}%
}%

\marginInfo*[Instructions]{Screw the Housing-Top and the assembled Housing-Front to the housing.}%

\marginTips*[Tip]{Before you screw the front panel to the housing, all cables should be connected inside the housing and the stepper motors should also be connected to the PCB. Also ensure that you flashed the firmware to the ESP32. I recommend a basic functionality test before closing the housing.}%

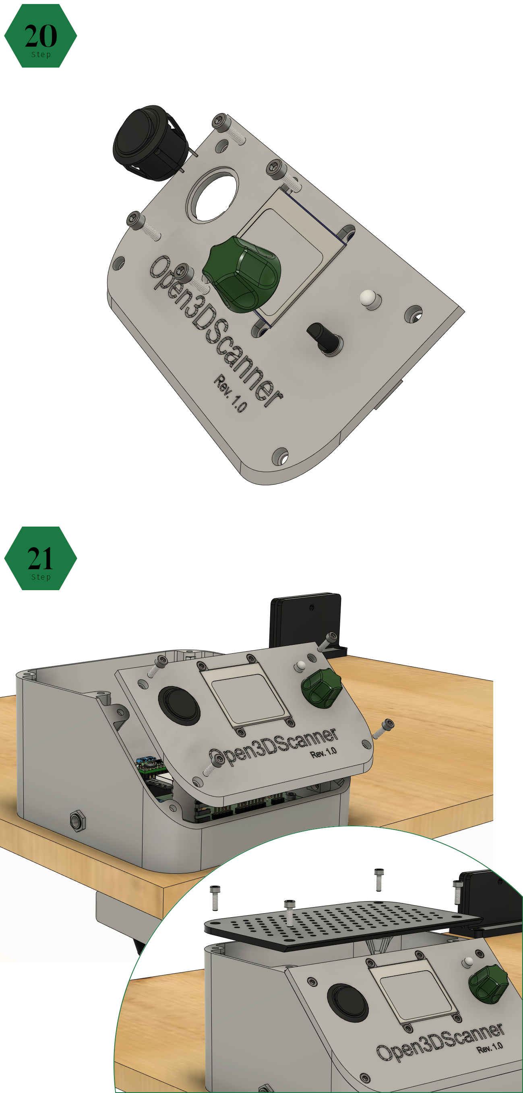
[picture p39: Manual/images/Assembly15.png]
%
{\captionof{figure}{Step 20 \& 21 of the Open3DScanner assembly}}
\clearpage%

% STEP 22 & 23
\sideTabularx[Required parts for step 22]{%
	\rowcolors{2}{tableLineTwo}{tableLineOne}% specify rowcolors in tabularx style
	\begin{tabularx} {\marginparwidth} {>{\rowmac \hsize=1.5\hsize}X>{\rowmac \hsize=0.5\hsize}X<{\clearrow}}%
		\tabularxHeader%
		Part & Quantity\\%
		4.0$\times$16 Countersunk Wood Screwt & 6\\%
	\end{tabularx}%
}%

\marginInfo*[Instructions]{Screw the assembled scanner onto the base plate.}%

\marginTips*[Tip]{For the exact alignment on the base plate, there is a detailed illustration at the end of the assembly instructions.}%

\sideTabularx[Required parts for step 23]{%
	\vspace{3.30cm}%
	\rowcolors{2}{tableLineTwo}{tableLineOne}% specify rowcolors in tabularx style
	\begin{tabularx} {\marginparwidth} {>{\rowmac \hsize=1.5\hsize}X>{\rowmac \hsize=0.5\hsize}X<{\clearrow}}%
		\tabularxHeader%
		Part & Quantity\\%
		4.0$\times$16 Countersunk Wood Screwt & 6\\%
	\end{tabularx}%
}%

\marginInfo*[Instructions]{Screw the assembled lights onto the base plate.}%

\marginTips*[Tip]{For the exact alignment on the base plate, there is a detailed illustration at the end of the assembly instructions.}%

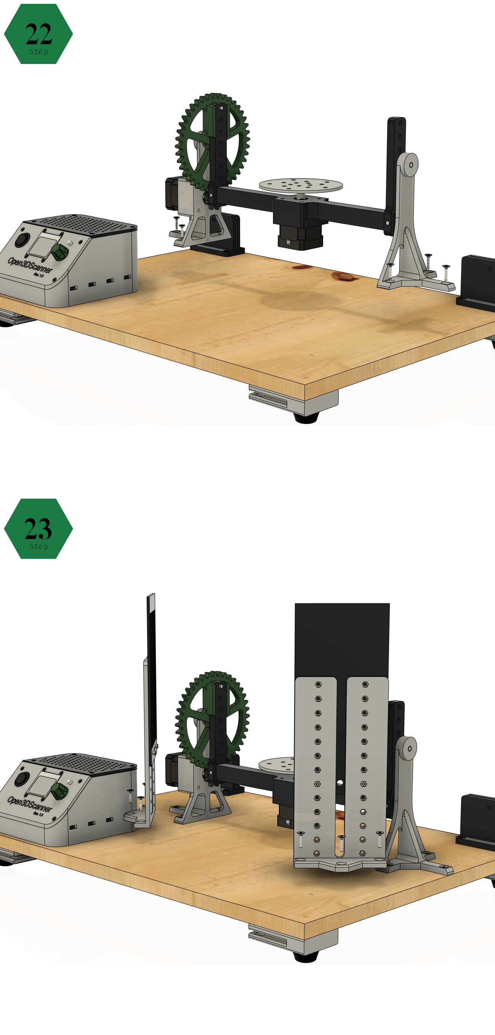
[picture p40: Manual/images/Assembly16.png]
%
{\captionof{figure}{Step 22 \& 23 of the Open3DScanner assembly}}
\clearpage%

% STEP 24 & Fin
\sideTabularx[Required parts for step 24]{%
	\rowcolors{2}{tableLineTwo}{tableLineOne}% specify rowcolors in tabularx style
	\begin{tabularx} {\marginparwidth} {>{\rowmac \hsize=1.5\hsize}X>{\rowmac \hsize=0.5\hsize}X<{\clearrow}}%
		\tabularxHeader%
		Part & Quantity\\%
		Cable-Holder & 5\\%
		4.0$\times$16 Countersunk Wood Screwt & 10\\%
	\end{tabularx}%
}%

\marginInfo*[Instructions]{Screw the cable holders onto the base plate.}%

\marginTips*[Tip]{For the exact alignment on the base plate, there is a detailed illustration at the end of the assembly instructions. All cables have to be routed for this step.}%

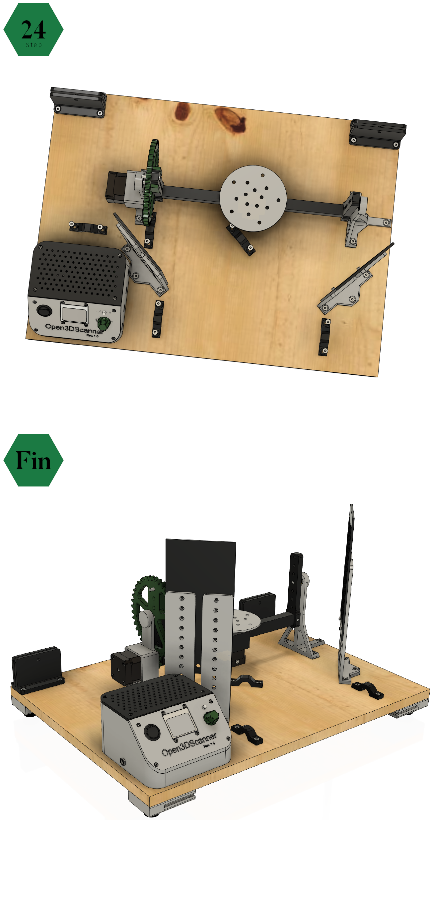
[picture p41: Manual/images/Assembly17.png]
%
{\captionof{figure}{Step 24 \& Fin of the Open3DScanner assembly}}
\clearpage%

% ALIGNMENT

\marginTips*[Tip]{This illustration is an aid for aligning the components on the base plate. All values are given in millimeters. For the individual setup, the values can deviate slightly, especially the distance between the two stands of the 3D scanner. This is due to the fact that a certain tolerance is given by the steel bars. Figure B shows the dimensions of the back plate.}%

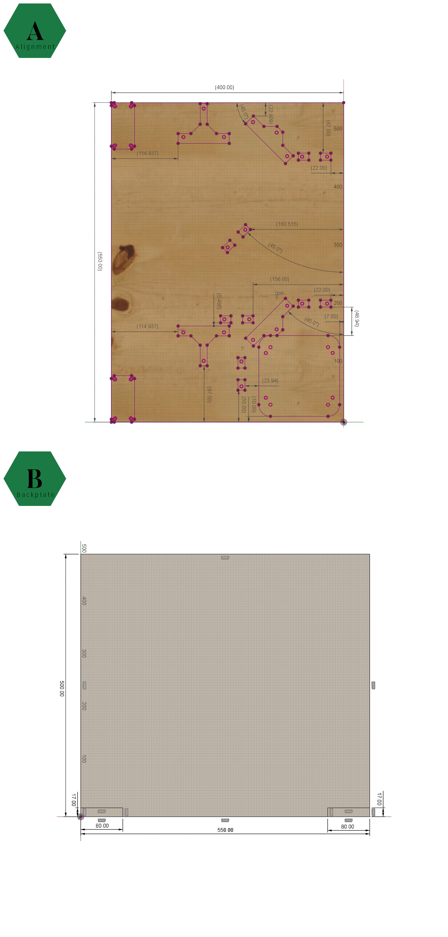
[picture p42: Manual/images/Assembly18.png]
%
{\captionof{figure}{Component Alignment on Base Plate \& Back Plate Size}}
\clearpage%

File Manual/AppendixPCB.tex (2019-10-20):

\chapter{Picture Series PCB Assembly}%
\label{cha:picSerPCB}%

This chapter contains a series of pictures that show step by step how the individual components are soldered onto the PCB.%

The images are completely uncommented, as they are not intended as instructions, but only as a reference.%

More detailed information on assembling the circuit board can be found in section~\ref{sec:assPCB}.%

It is quite possible that individual components may look different in your case, this applies especially to resistors and heat sinks. This is not a problem as long as the components are purchased to match the BOM.%

It is possible to use the pictures to determine the order in which the individual parts are assembled. However, this is not an instruction or obligation. Assemble the parts in the order that suits you best.%

\begin{figure}[ht!]%
	\begin{centered}%
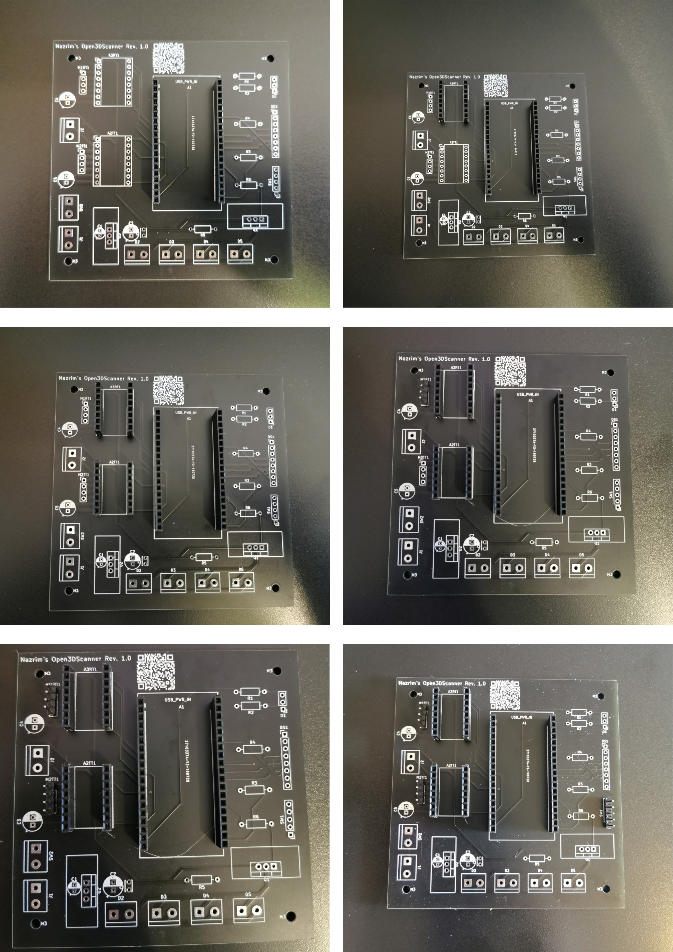
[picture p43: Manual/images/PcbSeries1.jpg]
		%
		\caption{Steps \numrange[text-rm=\lightBoldFont]{1}{6} of PCB assembly}%
	\end{centered}%
\end{figure}%

\begin{figure}[ht!]%
	\begin{centered}%
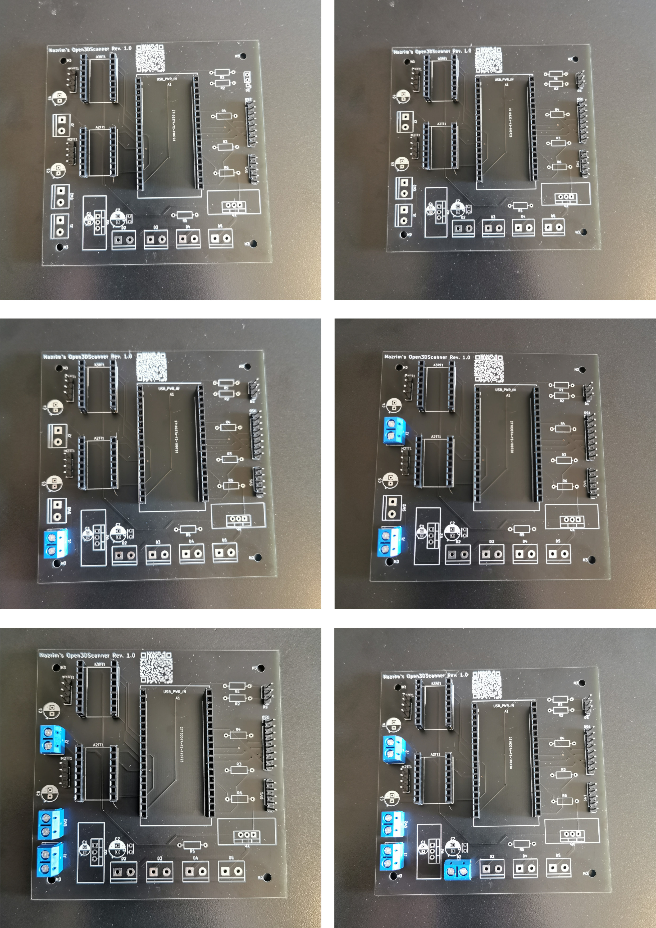
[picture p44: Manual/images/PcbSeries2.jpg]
		%
		\caption{Steps \numrange[text-rm=\lightBoldFont]{7}{12} of PCB assembly}%
	\end{centered}%
\end{figure}%

\begin{figure}[ht!]%
	\begin{centered}%
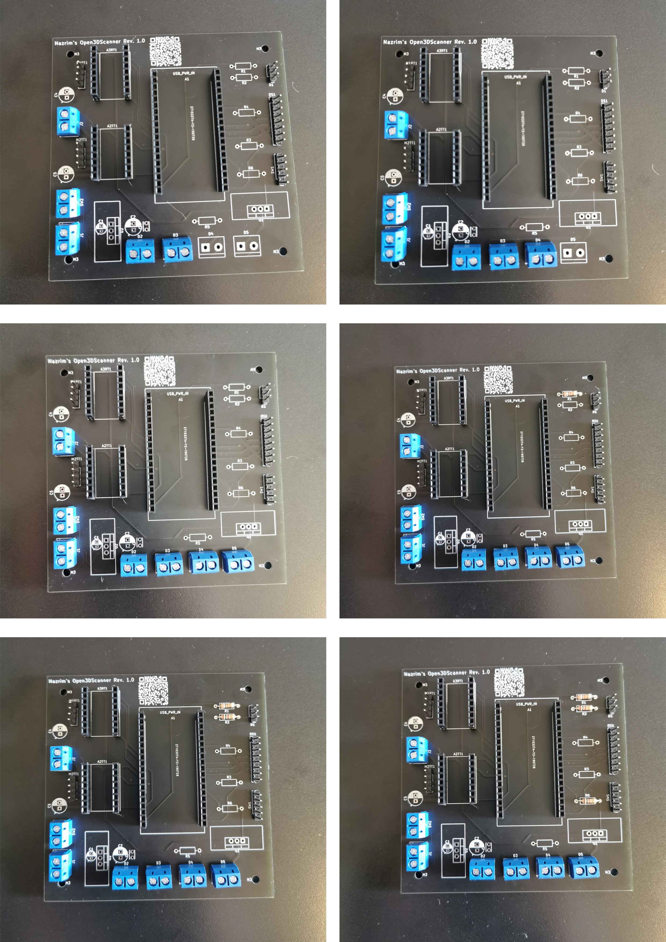
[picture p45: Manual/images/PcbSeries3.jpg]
		%
		\caption{Steps \numrange[text-rm=\lightBoldFont]{13}{18} of PCB assembly}%
	\end{centered}%
\end{figure}%

\begin{figure}[ht!]%
	\begin{centered}%
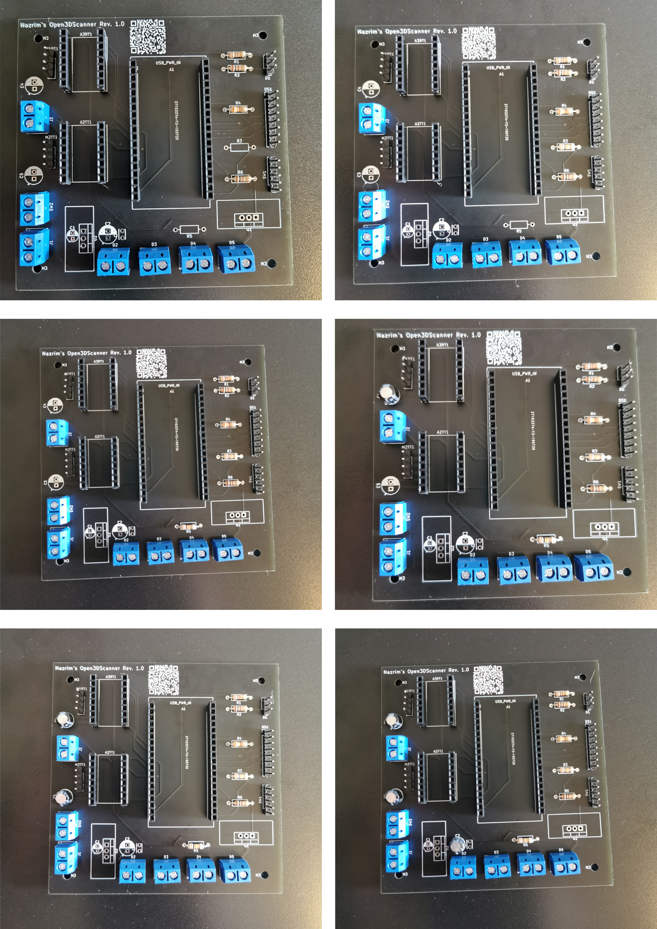
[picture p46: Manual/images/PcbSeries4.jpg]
		%
		\caption{Steps \numrange[text-rm=\lightBoldFont]{19}{24} of PCB assembly}%
	\end{centered}%
\end{figure}%

\begin{figure}[ht!]%
	\begin{centered}%
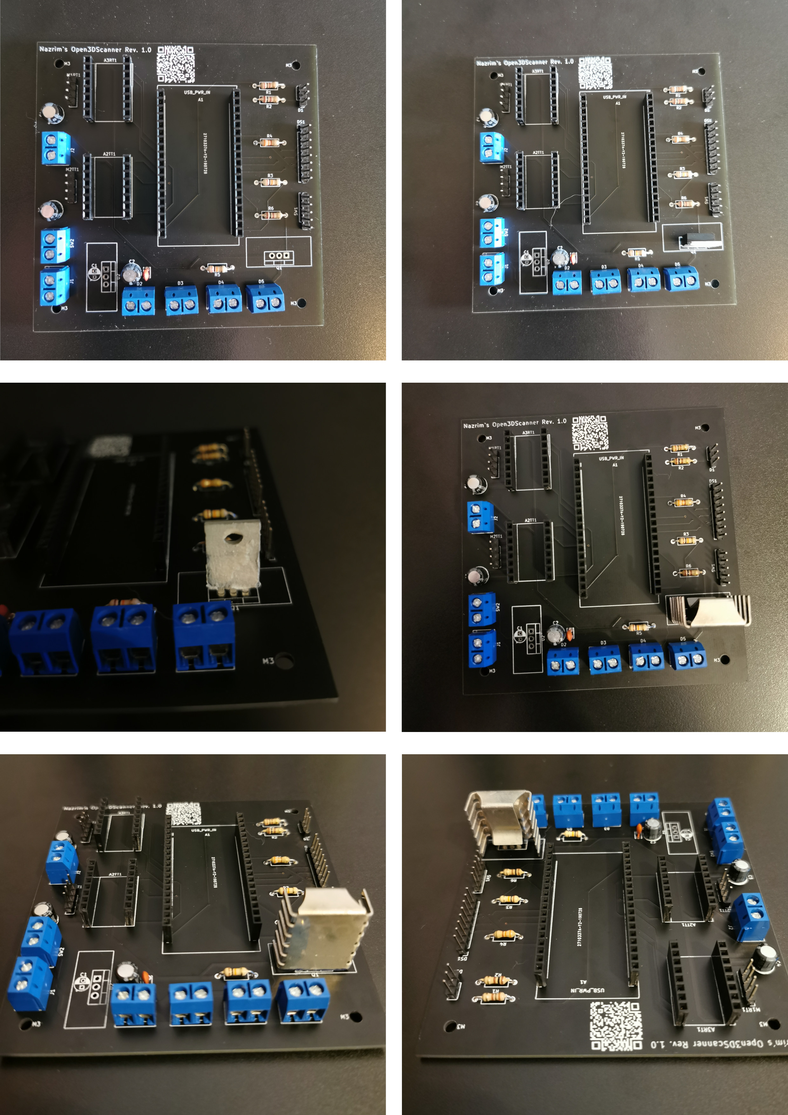
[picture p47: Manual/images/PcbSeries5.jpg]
		%
		\caption{Steps \numrange[text-rm=\lightBoldFont]{25}{30} of PCB assembly}%
	\end{centered}%
\end{figure}%

\begin{figure}[ht!]%
	\begin{centered}%
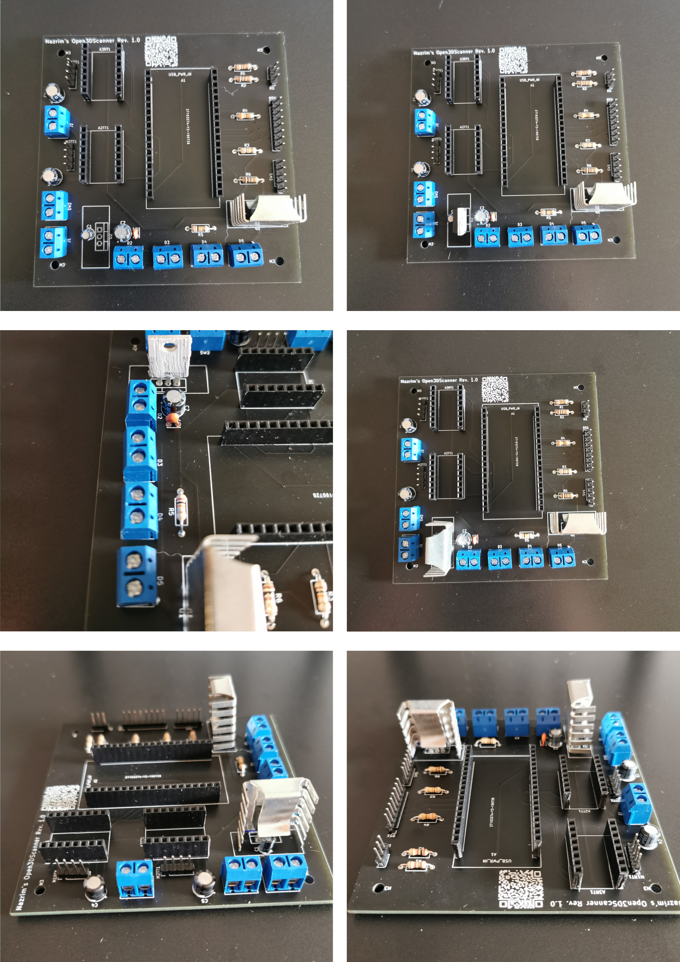
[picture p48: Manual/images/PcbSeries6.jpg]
		%
		\caption{Steps \numrange[text-rm=\lightBoldFont]{31}{36} of PCB assembly}%
	\end{centered}%
\end{figure}%

\begin{figure}[ht!]%
	\begin{centered}%
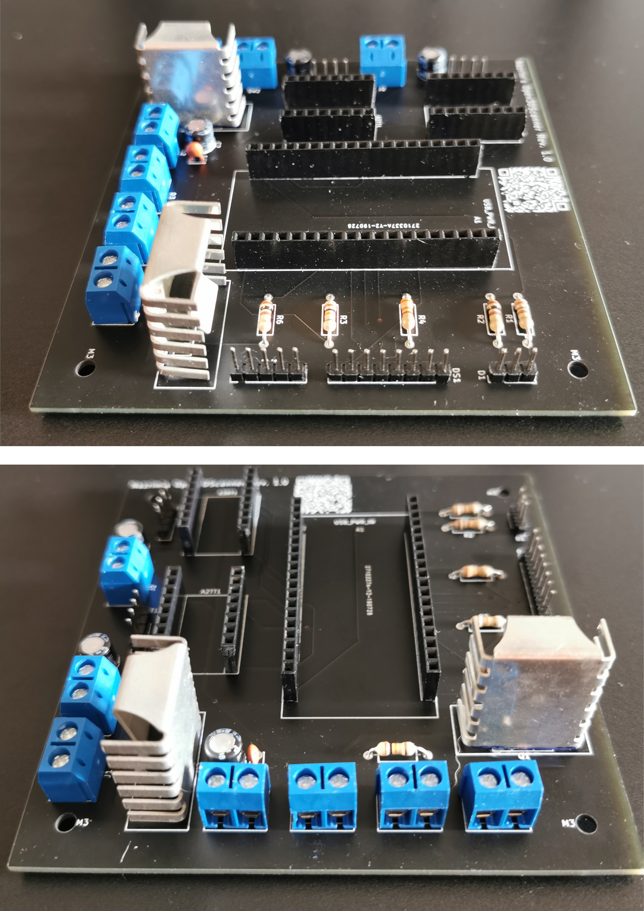
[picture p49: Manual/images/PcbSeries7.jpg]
		%
		\caption{Steps \numrange[text-rm=\lightBoldFont]{37}{38} of PCB assembly}%
	\end{centered}%
\end{figure}%

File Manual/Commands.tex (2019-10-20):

% This is a derivation of the \printMarginPartialToc command of yReport.cls which does not work (the way I want it) with reports
\DeclareDocumentCommand{\printMarginToc}{O{1} O{\partialTocTitle} o o}{%
	\mdfapptodefinestyle{partialToc}{%
		backgroundcolor=light-gray%
	}%
	\colorlet{partialTocColor}{mainColor}%
	\marginElement{%
		\IfValueT{#3}{\vspace*{#3}}%
		\begin{mdframed}[style=partialToc]%
			\alignLeftOrRightStandaloneInversed{\fontspec{Fira Sans Book}\Large #2}%
			{\color{partialTocColor}\hfill\rule{\linewidth}{.5mm}}%
			\vspace*{-2mm}%
			\printcontents[content]{partial}{0}{\setcounter{tocdepth}{#1}\hypersetup{linkcolor=black}}%
		\end{mdframed}%
		\IfValueT{#4}{\vspace*{#4}}%
	}%
}%

% use the toc style which is used by yReport for sections, for chapters too
\titlecontents{chapter}[0mm]% chapter style
{\contentsmargin[4mm]{0mm}\fontspec{Fira Sans Book}\alignLeftOrRightStandaloneInversed}%
{\isOddPage%
	{\makebox[3.5mm]{\color{partialTocColor}$\blacktriangleright$\hfill}}%
	{(p. \thecontentspage)}%
	\yTocSection}%
{}{}[\vspace*{-1mm}]%

\newcommand\setrow[1]{\gdef\rowmac{#1}#1\ignorespaces}% specify style of a tabularx row
\newcommand\clearrow{\global\let\rowmac\relax}% clear tabularx row style to default
\clearrow%
\newcommand{\tabularxHeader}{% table header style for tabularx tables
	\rowcolor{mainColor}%
	\setrow{\bfseries\sffamily\leavevmode\color{white}}%
}%
\rowcolors{2}{tableLineTwo}{tableLineOne}% specify rowcolors in tabularx style
\setlength{\extrarowheight}{1.5mm}% line separation between tabluarx rows

\makeatletter%
\DeclareDocumentCommand{\sideTabularx}{o m}{%
	\marginElement{%
		\strictpagechecktrue%
		\checkoddpage%
		\ifoddpage%
		\justifying\footnotesize%
		\else%
		\RaggedLeft\footnotesize%
		\fi%
		\@afterindentfalse\@afterheading%
		\vspace*{6mm} % compensate the table space added above the first line by the gape command
		#2%
		\captionsetup*[table]{font={footnotesize}}%
		\IfValueT{#1}{\captionof{table}{#1}}%
	}%
}%
\makeatother%

% small modifications to yReports titleTwo command
\makeatletter%
\DeclareDocumentCommand{\titleThree}{o o}{%
	\updateDarkMainColor%
	\thispagestyle{empty}%
	\symmetricalPage%
	\null%
	\tikzset{%
		fitting node/.style={%
			inner sep=0pt,%
			fill=none,%
			draw=none,%
			reset transform,%
			fit={(\pgf@pathminx,\pgf@pathminy) (\pgf@pathmaxx,\pgf@pathmaxy)}%
		},%
		reset transform/.code={\pgftransformreset}%
	}%
	\begin{tikzpicture}[remember picture, overlay]%
		% some coordinates
		\coordinate[yshift=-\titlepageHeaderHeight](rectangleEnd) at (current page.north east);%
		\coordinate[xshift=-4cm](dateCenter) at (rectangleEnd);%
		
		% draw an image if one was provided
		\IfValueT{#1}{\draw (current page.center)[yshift=-\titlepageHeaderHeight/2] node[align=center, inner sep=0mm, anchor=center] {\IfValueTF{#2}{}{}};}%
		
		% red rectangle
		\fill[mainColor] (current page.north west) rectangle (rectangleEnd) node[fitting node] (headerRectangle) {};%
		
		% title page text (title rule and subtitle)
		% title
		\draw (\leftmargin-9mm, -3cm) node[align=left, inner sep=0mm, anchor=south west, font=\fontsize{1.4cm}{1.2cm}\selectfont\chapterFont] (title) {%
			\hspace*{-.8mm}\begin{varwidth}{\textwidth}%
			\FlushLeft%
			\noHyphen\runtitle%
			\end{varwidth}%
		};%
		% rule
		\getwidthofnode{\titlepageTitleLength}{title}%
		\node[inner xsep=0mm, text width=\titlepageTitleLength+2mm, anchor=north west, yshift=-2mm, xshift=-1mm] (rule) at (title.south west) {{\color{White}\rule{\linewidth}{.6mm}}};%
		% author
		\node[inner xsep=0mm, text width=\linewidth, anchor=north west, yshift=-2mm] (subtitle) at (rule.south west) {
			{\fontsize{.6cm}{.72cm}\selectfont\color{White}%
				\@subtitle}% \runauthor
		};
		
		% Date
		\hexagon[mainColor]{dateCenter}{\dateRadius}%
		\hexagon[darkMainColor]{dateCenter}{\dateRadius}%
		\draw(dateCenter) node[text width=1.3cm, align=center] (day) {%
			\fontsize{1cm}{1.2cm}\selectfont\textbf{\twodigits{\the\day}}%
		};%
		\draw(dateCenter) node [node distance = .75cm, above of=day, text width=1.3cm, align=center](month) {\fontsize{.5cm}{1.2cm}\selectfont\textsc{\addfontfeatures{LetterSpace=10.0}\monthThreeLetterName}};%
		\draw(dateCenter) node[node distance = .65cm, below of=day, text width=1.3cm, align=center] (year) {\fontsize{.4cm}{1.2cm}\selectfont{\addfontfeatures{LetterSpace=20.0}\the\year} };%
		% author
		\node[anchor=south east] at ($(current page.south east)+(-6mm, 6mm)$) {\fontspec{Canter Light}\fontsize{10mm}{6mm}\color{White}\selectfont\@author};%
	\end{tikzpicture}%
	\null%
	\vfill%
	\newpage%
	\asymmetricalPage%
}
\makeatother%

\titleformat{\chapter}[block]%
{}% format
{% label
	{\darkMainColor}%
	\backgroundThisPageColor%
	\begin{tikzpicture}[remember picture, overlay]%
	\tikzfading[name=monfading,left color=transparent!100,right color=transparent!0]%
	\isOddPage{%
		\coordinate[xshift=-\bigVerticalLineWidth/2, yshift=-5.8cm] (numberCenter) at (current page.north east);%
	}{%
		\coordinate[xshift=\bigVerticalLineWidth/2, yshift=-5.8cm] (numberCenter) at (current page.north west);%
	}%
	\hexagon[darkMainColor]{numberCenter}{\chapterNumberRadius}%
	\node[yshift=2mm] at (numberCenter) (chapterNumber) {%
		\chapterNumberFont%
		\fontsize{\chapterNumberRadius}{\chapterNumberRadius}%
		\selectfont%
		\thechapter%
	};%
	\node [below=1mm of chapterNumber, text=Black!80] {%
		\addfontfeatures{LetterSpace=20.0}%
		\fontsize{1.2em}{1.4em}\selectfont%
		\chaptertitlename%
	};%
	\end{tikzpicture}%
}%
{0pt}% sep
{% code before
	\isOddPage{%
		\begin{FlushRight}%
			\vspace*{-1.5mm}%
	}{%
		\begin{FlushLeft}%
			\vspace*{-10mm}%
	}%
	\fontsize{1.8cm}{2.16cm}\chapterFont\selectfont%
}[% code after
	\alignLeftOrRightEnd%
]%

\hypersetup{%
	urlcolor=secondColor,%
	citecolor=secondColor,%
	linkcolor=secondColor%
}% Set link color to secondary color
\sisetup{mode = text}% Numbers and units from siunitx shall be displayed in normal text font

% Configure imakeidx package and href command to automatically build a href list
\makeindex[name=hrefs, title={References}, columns=1]%
\indexsetup{level=\chapter}%
\DeclareDocumentCommand{\hrefIdx}{m m}{%
	\href{#1}{#2}
	\index[hrefs]{
		\protect{%
			#2:\newline\href{#1}{%
				\texttt{%
					\replace{\markletters{#1}}{_}{\_}% iterate over all characters and add an empty hskip to allow line breaks at every character and then replace _ (subscript) with \_ (_ character)
				}%
			}%
		}%
	}%
}%

% Little helper function to ensure number x  with 0 <= x< 100 is always displayed with two digits (add a leading 0 if required)
\newcommand\twodigits[1]{%
	\ifnum#1<10 0#1\else #1\fi%
}%

% makro to iterate a string char by char
\def\xloop<#1#2>{%
	\ifx\relax#1%
	\else%
	#1\hskip0mm\xloop<#2>%
	\fi}%
\def\markletters#1{\xloop<#1\relax>}%

% Helper command for string replacements
\ExplSyntaxOn%
\NewDocumentCommand{\replace}{mmm}{%
	\marian_replace:nnn {#1} {#2} {#3}%
}%
\tl_new:N \l_marian_input_text_tl%
\cs_new_protected:Npn \marian_replace:nnn #1 #2 #3 {%
	\tl_set:Nn \l_marian_input_text_tl { #1 }%
	\tl_replace_all:Nnn \l_marian_input_text_tl { #2 } { #3 }%
	\tl_use:N \l_marian_input_text_tl%
}%
\ExplSyntaxOff%

% Format caption lables to use grey background on caption label and sideTitle format for caption itself
\DeclareCaptionLabelFormat{yLabel}{%
	{\raisebox{-1mm}{\normalsize\tikz{\node[anchor=west, inner sep=1mm, fill=lightGrey, font=\bfseries, text=mainColor] {#1 #2};}}\vspace{1mm}}{~}%
}%
\DeclareCaptionLabelFormat{yLabelFigure}{%
	{\raisebox{-1.5mm}{\normalsize\tikz{\node[anchor=west, inner sep=1mm, fill=lightGrey, font=\bfseries, text=mainColor] {#1 #2};}}\vspace{1mm}}{~}%
}%
\DeclareCaptionStyle{yReportCaptionStyleFigure}{labelsep=none, labelformat=yLabelFigure, singlelinecheck=false}%
\DeclareCaptionFormat{caption}{#1#2\lightBoldFont{#3}}%
\captionsetup*[figure]{style=yReportCaptionStyleFigure, justification=RaggedRight, position=bottom, format=caption}%
\captionsetup*[table]{style=yReportCaptionStyle, justification=RaggedRight, position=bottom, format=caption}%

% Allow to set side captions with label
\DeclareDocumentCommand{\sideCaptionOfL}{m m m}{\marginnote{\captionof{#1}{#2}\label{#3}}}

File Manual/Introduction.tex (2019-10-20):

\chapter{Preface}%
\label{c:preface}%
A 3D scanner is a good addition to a 3D printer.%

Before a detailed examination of the subject is performed, it is necessary to clarify what is the meaning of the term 3D scanning.%

\blockQuote[\hrefIdx{https://en.wikipedia.org/wiki/3D\_scanning}{3D scanning --- Wikipedia}]{3D scanning is the process of analyzing a real-world object or environment to collect data on its shape and possibly its appearance (e.g. colour). The collected data can then be used to construct digital 3D models.}%

3D scanning can greatly simplify the process of making a printed copy of an object. For example, when a component is broken and a 3D printer should be used to make a replacement. Or if a physical object for which no 3D files are available should be modified.%

While there are great 3D printers available for various budgets, the market for 3D scanners is not that big. At least the devices are not as common as 3D printers.%

Similar to 3D printing there are several technological approaches for the realization of 3D scanners, which are connected with different efforts and costs and show differences in the quality of the results.%

A particularly interesting approach for the average maker is photogrammetry. In photogrammetry a large number of photos from different viewing angles are taken from an object. Then a special software is used to create a 3D object from the images in a multi-stage process.\sideNote[white]{A great introduction to the photogrammetry pipeline, including references to scientific papers is provided by \hrefIdx{https://alicevision.org/\#photogrammetry}{AliceVision}.}%

Depending on the number and quality (illumination, sharpness, resolution, camera distance to object, \dots) of the images, an accurate 3D model of the physical model can be created.\sideNote[white]{Further information on the factors which affect the quality of the final model are explained by \hrefIdx{https://www.photomodeler.com/kb/factors\_affecting\_accuracy\_in\_photogramm/}{Pho\-to\-Mod\-el\-er Technologies}.} Theoretically, results with an accuracy of \SI{0.1}{\milli\meter} can be achieved.%

Since the cameras in smartphones (especially in high-end devices) are continuously being improved and nowadays deliver considerable quality, most people already have the most important tool for creating their own photogrammetry images.%

The other important tool in the photogrammetry pipeline is the software that processes the captured images and calculates the 3D model. There are many different software solutions which have been developed for photogrammetry.\sideNote{An extensive list of software for photogrammetry, which highlights some features for each software, is provided by  \hrefIdx{https://all3dp.com/1/best-photogrammetry-software/}{ALL3DP}.} Fortunately, there are also several open source projects in this list.%

All that is missing is a computer (as powerful as possible) that runs the software. This shouldn't be a problem because most makers already have a home computer.%

Thus for many makers all necessary tools are available to create 3D scans with photogrammetry. So the question arises why 3D scanning has such a low popularity compared to 3D printing. One possible answer to this question is that there is simply no need for it. Another possible answer is that the manual creation of the many photos that are needed will discourage most people because it is very time-consuming. Perhaps it is also because a 3D scanner is used much less often than a 3D printer, which is why one does not want to buy a 3D scanner, even if it is similarly inexpensive as a 3D printer.\sideNote{An overview of a large number of available 3D scanners and some of their features can be viewed at  \hrefIdx{https://www.aniwaa.com/comparison/3d-scanners/}{ANIWAA}. The list contains photogrammetry devices as well as various other technologies, but it is possible to filter the displayed devices.}%

For this reason the Open3DScanner project was started. The goal of the project is to provide the maker community with a 3D scanner that delivers 3D scans in good quality while keeping costs as low as possible by relying on existing tools such as smartphones and computers. It should be possible to implement the entire project for less than \SI[round-precision=2,round-mode=places,round-integer-to-decimal]{150}[\$], provided the necessary tools are available and the required parts can be procured without extreme (e.g. shipping) costs.%

In its standard configuration, the Open3DScanner offers a scanning area that includes a cylinder with a diameter of approximately \SI{26}{\centi\meter} and a height of approximately \SI{16}{\centi\meter}. This restriction can easily be circumvented to a certain extent by configuring the scans accordingly. Detailed information can be found in chapter~\ref{c:performingScans}. All parts are designed to fit on the print bed of an original Prusa i3 to allow the use of a variety of 3D printers.%

This document serves as a complete reference for the Open3DScanner project. It contains all the necessary information that makers need to build their own Open3DScanner, modify the 3D scanner, or simply get detailed information about the project.%

Before a detailed examination of the Open3DScanner, chapter~\ref{c:rel_projects} introduces other open source 3D scanners and compares them with the Open3DScanner. Chapter~\ref{c:usedSoftware} describes the toolchain used to create and design the Open3DScanner and shows dependencies to other projects (e.g. software libraries). Chapter~\ref{c:bom} contains a BOM, which contains all parts needed to build the Open3DScanner. In addition, the required tools for building the scanner are listed and hardware required for operation is described. Chapter~\ref{c:build} then describes in detail all the steps necessary to build your own Open3DScanner from the individual components. Chapter~\ref{c:userGuide} contains a user manual which describes the use of the fully assembled Open3DScanner. Finally, chapter~\ref{c:performingScans} presents various tips and tricks that make it easier to create successful 3D scans using photogrammetry.%

Thus, depending on the interests of the reader, not all chapters are equally interesting. However, the structure of the document should allow the chapters to be read individually and independently of each other. The necessary cross-references can be found in the necessary places.%

There is no schedule for future development of this project. They are based on my needs and the needs of the Open3DScanner users.%

The Open3DScanner has been published in various communities to reach a wider audience. The center of development and secure reference point for the latest version of the project is the {\faGithub} \hrefIdx{https://github.com/nazzrim/Open3DScanner}{Open3DScanner repository}.%

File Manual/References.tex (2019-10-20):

\chapter[Used Software, Tools, etc.]{Used Software, Tools, etc.}%
\label{c:usedSoftware}%
This chapter provides an overview of the software and tools used to implement the Open3DScanner project. Furthermore used artefacts (libraries, 3D models, \dots) as well as the corresponding licenses are presented.%

The aim is to create an as complete as possible list of the dependencies of the Open3DScanner in order to have all relevant license information at one central location.%

Transitive dependencies, which result from the used artefacts, are excluded from the consideration. If you are interested, please refer to the documentation of the respective artifact, which is linked at the appropriate place of this document, if available.%

\section{Arduino}%
Since the heart of the Open3DScanner is an ESP32\sideNote[white]{Detailed information about the ESP32, including its data sheet, can be found on the \hrefIdx{https://www.espressif.com/en/products/hardware/esp32/overview}{Espressif ESP32 product page}.} and the development should be done with the \hrefIdx{https://www.arduino.cc/en/main/software}{Arduino IDE}, one of the most important dependencies in the Arduino area is the {\faGithub} \hrefIdx{https://github.com/espressif/arduino-esp32}{Arduino core for ESP32 WiFi chip}, which allows the use of ESP32 development boards with the Arduino IDE. This simplifies the development of the project considerably.%

The Arduino IDE is released under the GPL license, while the included libraries are released under the LGPL license. The LGPL license is also applied to the Arduino core for the ESP32 WiFi chip.%

\subsection{Libraries}%
In the following the libraries which were used for the implementation of the Open3DScanner and are not included in the Arduino IDE are described.%

\begin{table}[ht!]%
	\begin{centered}%
		\rowcolors{2}{tableLineTwo}{tableLineOne}% specify rowcolors in tabularx style
		\begin{tabularx} {\linewidth} {>{\rowmac \hsize=1.3\hsize}X>{\rowmac \hsize=0.5\hsize}X>{\rowmac \hsize=0.9\hsize}X>{\rowmac \hsize=0.8\hsize}X>{\rowmac \hsize=1.5\hsize}X<{\clearrow}}%
			\tabularxHeader%
			Library & Version & Author & License & Purpose\\%
			{\faGithub} \hrefIdx{https://github.com/platisd/nokia-5110-lcd-library}{nokia-5110-lcd-library} & 2.0.0 & platisd & MIT License & Driving the Nokia 5110 LCD.\\%
			{\faGithub} \hrefIdx{https://github.com/laurb9/StepperDriver}{StepperDriver} & 1.1.4 & laurb9 & not specified & Two-pin stepper motor driver library.\\%
			{\faGithub} \hrefIdx{https://github.com/madhephaestus/ESP32Encoder/}{ESP32Encoder} & 0.1.5 & madhephaestus  & MIT License & Rotary encoder library using interrupts.\\%
			{\faGithub} \hrefIdx{https://github.com/jonblack/arduino-menusystem}{arduino-menusystem} & 3.0.0 & jonblack & MIT License & Ddata structures for menu structures.\\%
		\end{tabularx}%
		\caption{Arduino Libraries used within the Open3DScanner}%
	\end{centered}%
\end{table}%

It can be seen that only a few external libraries are required in total, since a large part of the functionality is already available through the libraries provided by the Arduino IDE and the Arduino core for ESP32 WiFi chip.%

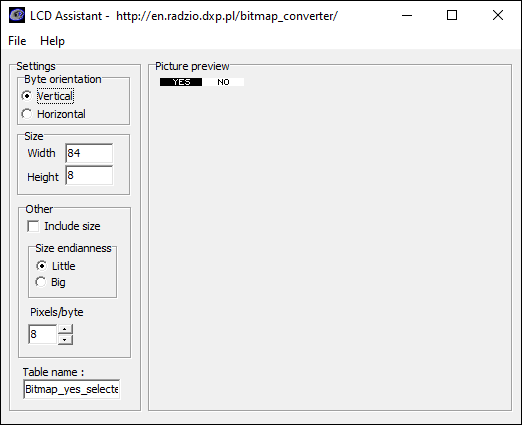
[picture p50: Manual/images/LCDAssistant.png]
\marginElement{\captionof{figure}{LCDAssistant GUI}}%

In some places the display of the Open3DScanner shows other things as pure text, e.g. to show buttons. For this purpose, corresponding bitmaps were created, which were then translated into corresponding character arrays with the tool \hrefIdx{http://en.radzio.dxp.pl/bitmap_converter/}{LCD Assistant}\marginInfo[LCDAssistant]{The LCDAssistant is a useful tool that allows the easy transformation of bitmaps into character arrays, which can directly fed to the various LCD screens. It provides some configuration to match different LCDs.} from Radosław Kwiecień.%

The license of the LCD Assistant is not specified by the developer on the project page.%

\section{Schematics and PCB Design}%
Although it is practical to test the necessary circuits on a solderless breadboard during development, this is not a long-term solution. This is especially true if you consider that the breadboard creates new sources of error.%

In addition to the generally known problems, such as instability (in general, but also with e.g. vibrations) and high space requirements compared to a custom PCB, it must be noted that the individual tracks of the breadboard have high resistances and can introduce unwanted capacitances into the circuit\sideNote{More information about unwanted side effects that can occur when using breadboards can be found on \hrefIdx{https://hackaday.com/2016/01/19/solderless-breadboard-parasitics/}{Hackaday} and \hrefIdx{https://breadboardadventures.com/2016/02/14/a-square-and-triangle-wave-vco-part-ii-taming-the-voltage-spikes/}{Breadboard Adventures}.}.%

During development it was not possible to use an LDO\sideNote{Low Dropout} regulator on the breadboard and to get a stable output voltage of \SI{5}{\volt}. Instead it was necessary to outsource the low-dropout and its components to a prototype PCB to get a stable output voltage. Otherwise, it would not have been possible to test the circuit design, as spontaneous voltage drops led to crashes of the ESP32.%

Figure~\ref{f:breadboard} shows the circuit of the Open3DScanner on a breadboard. In addition the prototype PCB with the LDO regulator is visible. It's easy to see that the circuit is chaotic and therefore difficult to maintain, debug, and develop. For the picture even cables have been removed: The stepper motors are not connected and the lights have been removed.%

Due to the size of the components it was necessary to use two breadboards, which makes the whole construction extremely fragile. More than 50 cables were needed to build the circuit on the breadboards.%

\begin{figure}[ht!]%
	\begin{centered}%
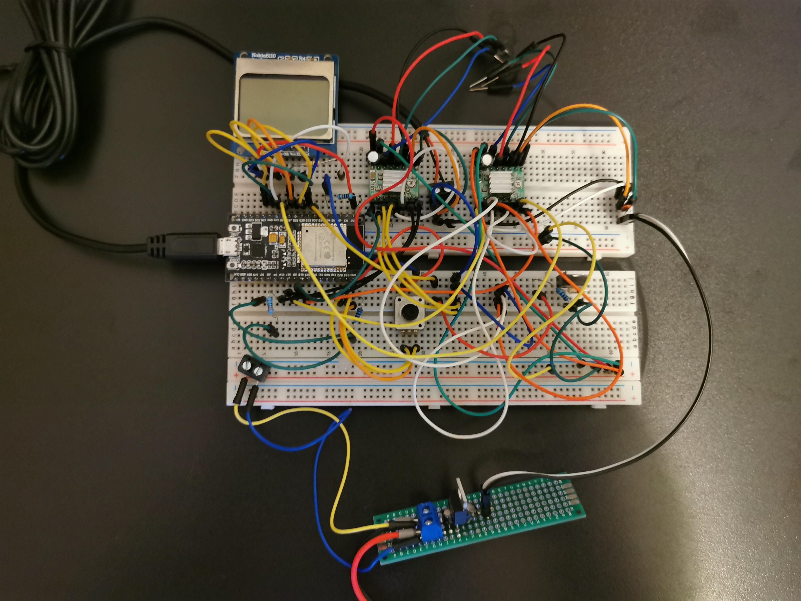
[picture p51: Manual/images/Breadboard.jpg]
		%
		\caption{The Open3DScanner circuit on a solderless Breadboard}%
		\label{f:breadboard}%
	\end{centered}%
\end{figure}%

It quickly becomes clear that in the long run it is necessary to design and manufacture\marginTips[JLCPCP]{The PCBs for the first prototype of the Open3DScanner were manufactured by \hrefIdx{https://jlcpcb.com/}{JLCPBP}. The manufacturer is located in China and offers very cheap PCBs, which were of very good quality when I ordered them. The only disadvantage, besides the minimum order of 5 boards, is that even the fastest shipping takes about a week. However, this is more than compensated when comparing prices with local suppliers.} a special PCB for the Open3DScanner.%

For the design of the board the software \hrefIdx{http://www.kicad-pcb.org/}{KiCad} was used.  KiCad is an open source program package licensed under the GPL.%

KiCad contains tools for all steps involved in designing a PCB. The individual tools offer very good integration with each other, which simplifies the design process considerably.%

First you create a schematic diagram for the circuit. The individual components are connected with so-called footprints. These footprints define the layout of the individual components on the board (holes, labels, \dots). With this information you go over to the actual design of the PCB. Figure~\ref{f:schematic} shows the schematic diagram for the Open3DScanner.%

\begin{figure}[ht!]%
		\sideCaptionOfL{figure}{Schematic diagram for the Open3DScanner designed in KiCad}{f:schematic}%
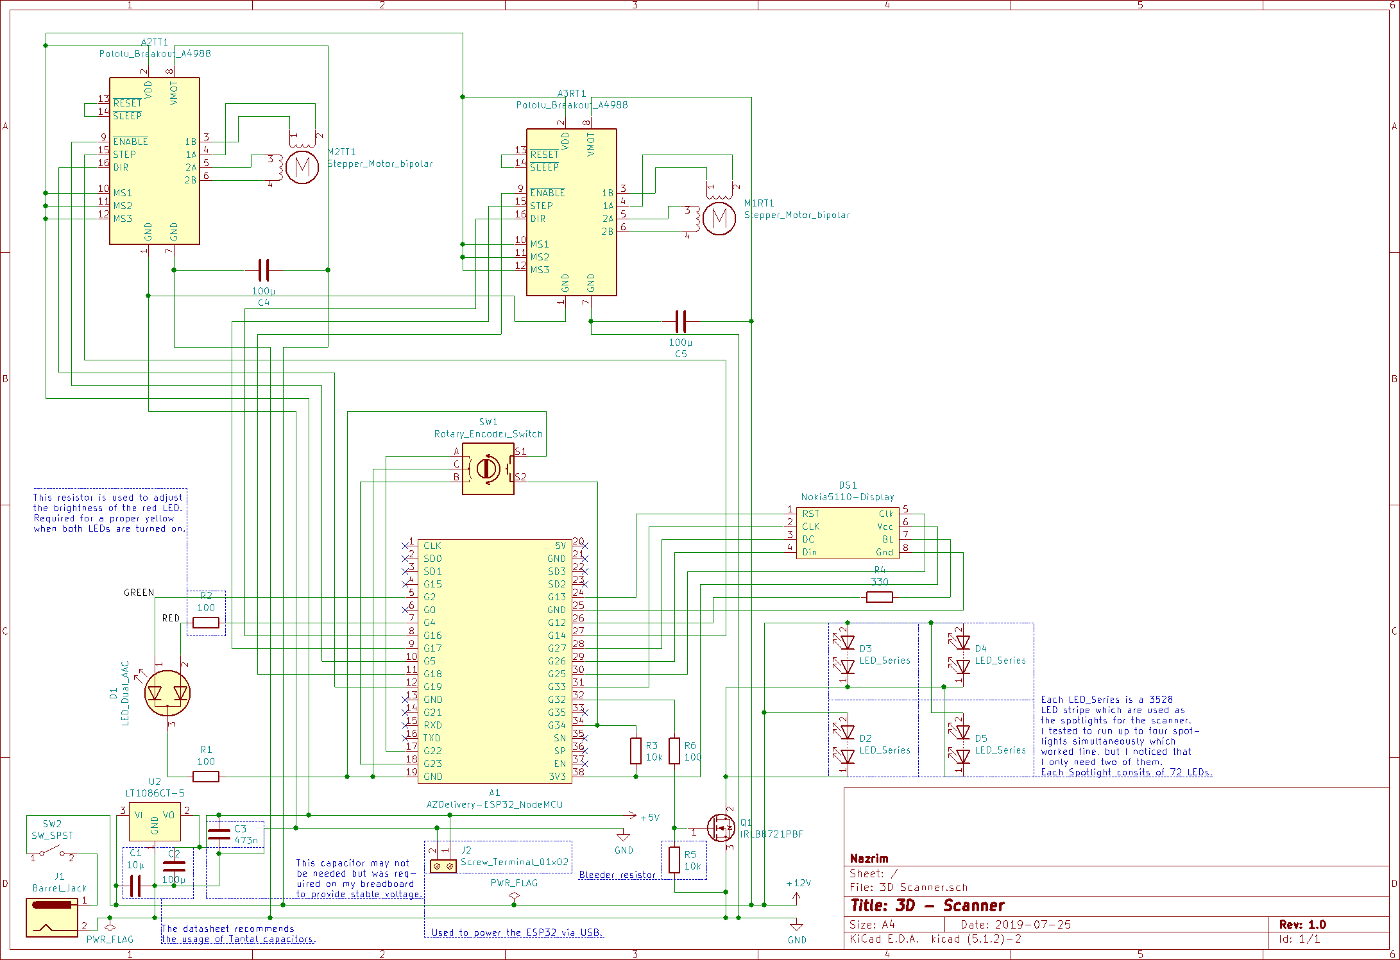
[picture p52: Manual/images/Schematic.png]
		%
\end{figure}%

All elements are placed on an empty surface, which represents the later board. The user now has to position the individual elements and draw traces for the connections. The user is always shown which pins have to be connected to each other. Figure~\ref{f:pcb} shows the PCB design for the Open3DScanner.%

\begin{figure}[ht!]%
		\sideCaptionOfL{figure}{PCB design for the Open3DScanner designed in KiCad}{f:pcb}%
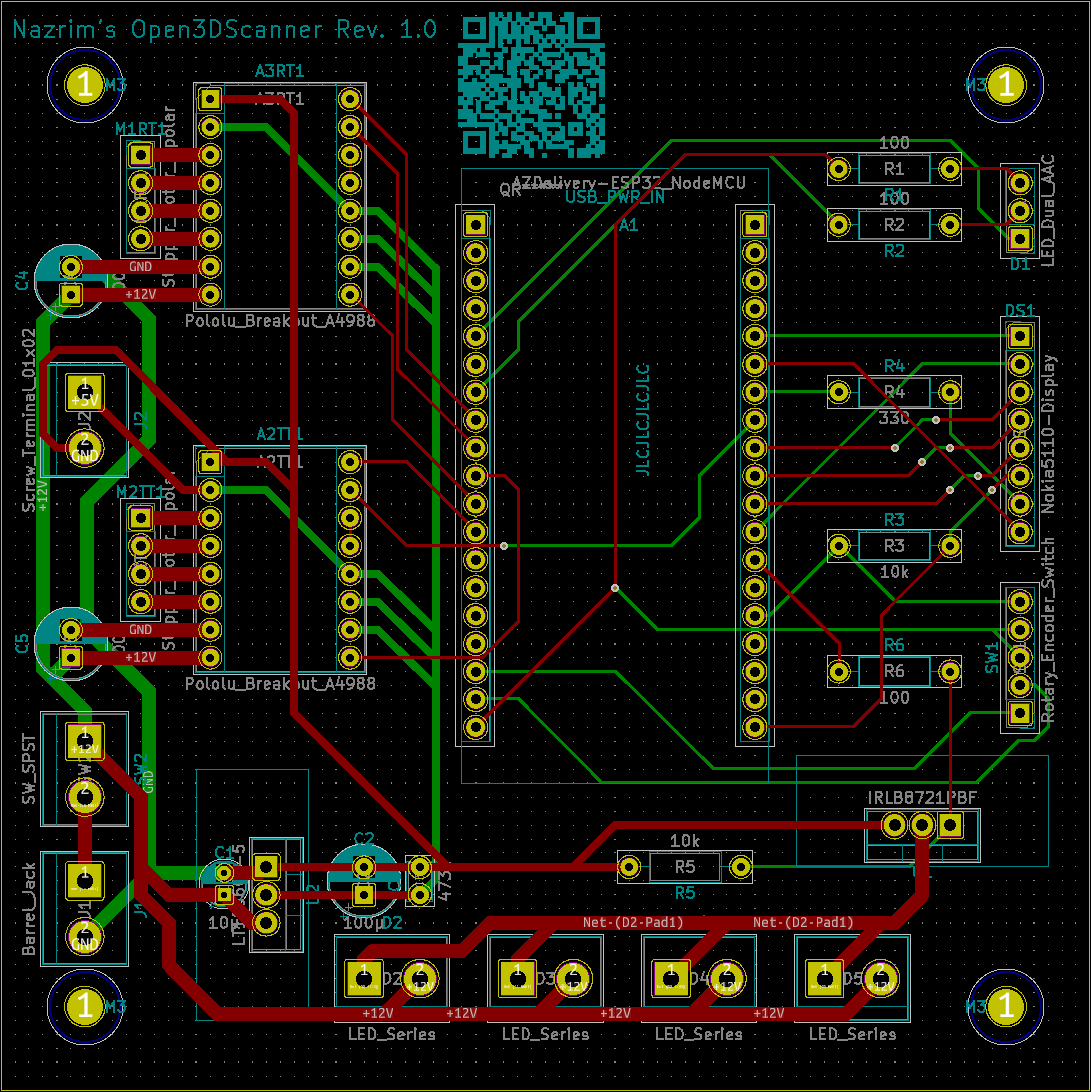
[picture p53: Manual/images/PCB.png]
		%
\end{figure}%

At this point all necessary steps for the design of the PCB are completed. The necessary Gerber files\marginInfo[Gerber Files]{Manufacturers generally provide instructions on which Gerber files to use and which naming conventions to follow. Often there are even instructions for concrete software.} can be generated and handed over to an appropriate service provider for production.%

Alternatively, a 3D model of the finished board (with all components) can be created beforehand. For this it is necessary to link the footprints with 3D models. For the rendering of the 3D model no further effort is necessary.%

I consider this step very useful. On the one hand you get a better idea of what the finished board will look like and on the other hand you can check again that no components are in conflict with each other. This is especially important in case of a high packing density of the components. Figure~\ref{f:render} shows the rendered 3D model of the Open3DScanner's board including all components.%

\begin{figure}[ht!]%
	\sideCaptionOfL{figure}{3D rendering of the PCB including components for the Open3DScanner designed in KiCad}{f:render}%
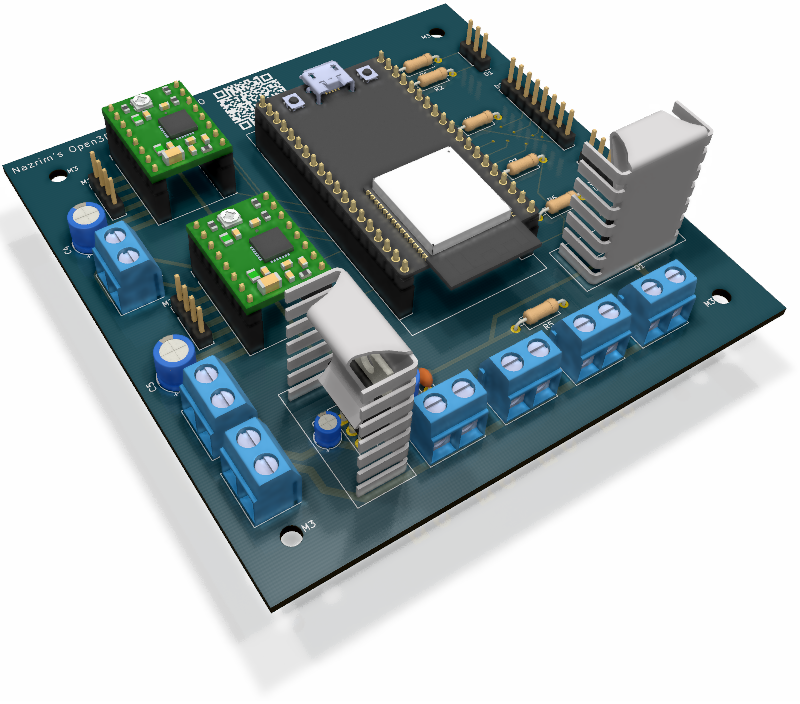
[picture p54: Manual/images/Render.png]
	%
\end{figure}%

Due to the large number of existing components, KiCad cannot contain a schematic symbol, footprint, and 3D model for all of them. It is also possible that a different footprint should be selected for a component, for example because it is not connected directly to the board, but via a pin header.%

This also applied to several parts of the Open3DScanner. In case of missing schematic symbols and footprints, it is possible to draw the corresponding parts via intuitive integrated editors.%

If 3D models for components are missing, it is necessary to provide them (for example as STEP file). If this does not happen, the board can still be rendered, but the corresponding part locations remain empty.%

A possible source for corresponding 3D models of components to be used in open source projects is  \hrefIdx{https://grabcad.com/library}{GrabCAD}\marginCritical[GrabCAD License]{3D models obtained from GrabCAD may only be used for non-commercial purposes. For commercial use, permission must be obtained from the author of the model.}. For licensing reasons I prefer other sources for obtaining 3D models of components. On the one hand many manufacturers already provide corresponding CAD files and on the other hand \hrefIdx{https://www.snapeda.com/}{SnapEDA} offers a large database of components containing a schematic symbol, a PCB footprint, and a 3D model. The individual entries are licensed under CC-BY-SA 4.0.%

\subsection{Used 3D Models}%
This section lists the 3D models which are not already part of KiCad and which are used to render the Open3DScanner board and their source.%

\begin{table}[ht!]%
		\sideCaptionOf{table}{3D Models used for rendering the Open3DScanner}%
		\rowcolors{2}{tableLineTwo}{tableLineOne}% specify rowcolors in tabularx style
		\begin{tabularx} {\linewidth} {>{\rowmac \hsize=\hsize}X>{\rowmac \hsize=\hsize}X<{\clearrow}}%
			\tabularxHeader%
			Component & Source\\%
			ESP32 Devkit-C  & \href{https://www.snapeda.com/parts/ESP32-DEVKITC-32D/Espressif\%20Systems/view-part/}{SnapEDA - ESP32-DEVKITC-32D}\\%
			Blue two pole screw terminal & \hrefIdx{https://www.snapeda.com/parts/TB002-500-02BE/CUI\%20Inc./view-part/}{SnapEDA - TB002-500-02BE}\\%
			A4988 stepper driver & \hrefIdx{https://www.pololu.com/product/1182}{Pololu - A4988 product page}\\%
			TO 220 attachable heatsink & \hrefIdx{https://www.fischerelektronik.de/web\_fischer/en\_GB/heatsinks/C02/Attachable\%20heatsink/PG/FK245MI247O/search.xhtml}{fischer elektronik - FK 245 MI 247 O product page}\\%
		\end{tabularx}%
\end{table}%

\section{3D Design}%
When it comes to the 3D modeling of the Open3DScanner, there is little special to mention.%

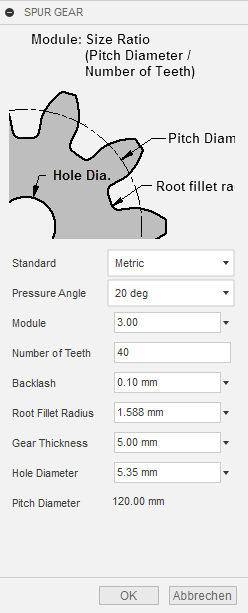
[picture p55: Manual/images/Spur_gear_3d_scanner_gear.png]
\marginElement{\captionof{figure}{Fusion 360 script settings for creating the Open3DScanner's spur gear}}%

All components needed for the project and printed with a 3D printer were designed with \hrefIdx{https://www.autodesk.de/products/fusion-360/overview}{Fusion 360}. It should be noted that Fusion 360 contains handy scripts to create certain elements automatically. One of these scripts allows the creation of gears with given parameters. This script was used for the gears in the Open3DScanner.%

CAD models of some standard components such as ball bearings are required for the subsequent building instructions and render images of the finished Open3DScanner.%

\begin{table}[ht!]%
	\rowcolors{2}{tableLineTwo}{tableLineOne}% specify rowcolors in tabularx style
	\begin{tabularx} {\linewidth} {>{\rowmac \hsize=1.2\hsize}X>{\rowmac \hsize=0.9\hsize}X>{\rowmac \hsize=0.9\hsize}X<{\clearrow}}%
		\tabularxHeader%
		Source & Model Type & License\\%
		\hrefIdx{https://www.astbearings.com/free-3d-cad-models-for-bearings.html}{AST Bearings} & Bearings & not specified, but free\\%
		\faGithub{} \hrefIdx{https://github.com/Hecatron-Machines/Cad.Solidworks.Parts}{Cad.Solidworks.Parts}& Nema 17 & MIT\\%
		\hrefIdx{https://octopart.com/terms}{Octopart} & Various & not specified, but free\\%
		\faGithub{} \hrefIdx{https://github.com/FreeCAD/FreeCAD-library}{FreeCAD-library}& Dupont Connectors & CC-BY 3.0\\%
		\hrefIdx{https://www.digikey.de//resources/3d-models}{Digi-Key}& Molex Connectors \& Cable Lugs & not specified, but free\\%
		\hrefIdx{https://www.snapeda.com/}{SnapEDA}& Micro USB-B Connector & CC-BY-SA 4.0\\%
	\end{tabularx}%
	\caption{Sources for CAD models of non-electrical components}%
	\label{t:cad}%
\end{table}%

There are several vendors with large libraries of CAD models, which may not be freely used and/or distributed. Table~\ref{t:cad} contains information which offers were used for which models.%

\section{Photogrammetry}%
\label{sec:photogrammetry}
The heart of the entire photogrammetry process is the software that creates the 3D model from the images taken.%

For this purpose I use the software \hrefIdx{https://alicevision.org/\#meshroom}{Meshroom}. It is intuitive to use and performs the entire process. The finished (textured) 3D model is created from the fed-in images. Alternative software solutions do not always offer the entire process and generate for example only a point cloud, which has to be converted into a 3D model with another program. This applies for example to \hrefIdx{http://ccwu.me/vsfm/}{VisualSFM}.%

Meshroom is released under the MPL 2.0 and can be compiled by the user or can be obtained as a ready-to-use installer.%

In general, I would recommend the use of Meshroom to anyone, simply because it is very easy to use and produces great results while offering extensive configuration options.%

The only limitation is that a CUDA-enabled graphics card (Nvidia) is required for optimal results, as the calculations are done on the GPU. If such a card is not available, a "preview mode" can be activated, which works without CUDA, but also produces worse results.%

\section{\LaTeX}%
\LaTeX{} was used to create this manual and last but not least we will look at which packages were used to create it.%

The document class used is yReport from Harvey Sheppard. The class is part of his project {\faGithub} \hrefIdx{https://github.com/HarveySheppard/yLaTeX}{yLatex}, which provides document classes and packages to create appealing documents. The entire yLatex project is licensed with LPPL 1.3.%

The compiler used is \hrefIdx{http://www.tug.org/xetex/}{\hologo{XeLaTeX}}, which is required by the document class yReport. \hrefIdx{https://www.tug.org/texlive/}{\hologo{TeX} Live} is used as \hologo{TeX} distribution and \hrefIdx{https://www.texstudio.org/}{\hologo{TeX}studio} as editor.%

Pictures can be found in various places in this document. If these images are not photos, screenshots, or exports from other software, the images were created with Gimp which is licensed under the GPL.%

In addition, various packages are used to realize individual aspects of the document. These are listed below.%

\begin{table}[ht!]%
	\begin{centered}%
		\rowcolors{2}{tableLineTwo}{tableLineOne}% specify rowcolors in tabularx style
		\begin{tabularx} {\linewidth} {>{\rowmac \hsize=1.0\hsize}X>{\rowmac \hsize=0.7\hsize}X>{\rowmac \hsize=1.0\hsize}X>{\rowmac \hsize=0.5\hsize}X>{\rowmac \hsize=1.8\hsize}X<{\clearrow}}%
			\tabularxHeader%
			Package & Version & Maintainer & License & Purpose\\%
			\hrefIdx{https://ctan.org/pkg/fontawesome}{fontawesome5}  & 5.9.0 & Marcel Krüger & LPPL 1.3c \& OFL & Required by yAuthorBlock and used to show some icons across the document.\\%
			{\faGithub} \hrefIdx{https://github.com/HarveySheppard/yLaTeX}{yAuthorBlock}  & unknown & Harvey Sheppard & LPPL 1.3 & Used to create the author block on the second page.\\%
			\hrefIdx{https://ctan.org/pkg/tabularx}{tabularx}  & 2.11 & The \LaTeX{} Team & LPPL 1.3 & Since tabu (used by yReport) is somewhat buggy, this document uses tabularx.\\%
			\hrefIdx{https://ctan.org/pkg/siunitx}{siunitx}  & 2.7s & Joseph Wright & LPPL 1.3c & Used to display numbers and units in a proper way.\\%
			\hrefIdx{https://ctan.org/pkg/indextools}{indextools}  & 1.5.1 & Maïeul Rouquette & LPPL 1.3 & Used to build an index of all weblinks for printed documents.\\%
			\hrefIdx{https://ctan.org/pkg/xparse}{xparse} & 2019-05-28 & The \LaTeX{} Team & LPPL 1.3c & Required for string magic to display urls in the index (Appendix~\ref{ca:refs}) in a proper way.\\%
			{\faGithub} \hrefIdx{https://github.com/HarveySheppard/yLaTeX}{infoBulle}  & unknown & Harvey Sheppard & LPPL 1.3 & Used for displaying various block types (info, warning, \dots) in main area.\\%
			{\faGithub} \hrefIdx{https://github.com/HarveySheppard/yLaTeX}{marginInfoBulle}  & unknown & Harvey Sheppard & LPPL 1.3 & Used for displaying various block types (info, warning, \dots) in margin area.\\%
			\hrefIdx{https://ctan.org/pkg/isodate}{isodate}  & 2.28 & Harald Harders & LPPL 1.3c & Used for uniform displaying dates. Required because of strange behaviour of datetime package (included in yReport).\\%
			\hrefIdx{https://ctan.org/pkg/xurl}{xurl}  & 0.07 & Herbert Vo\ss{} & LPPL 1.3 & Allow URL breaks at any alphanumerical character.\\%
			\hrefIdx{https://ctan.org/pkg/hologo}{hologo}  & 1.13 & Heiko Oberdiek & LPPL 1.3 & Used to disaplay logos from the \LaTeX{} family.\\%
		\end{tabularx}%
		\caption{Used \LaTeX{} packages within the Open3DScanner's manual}%
	\end{centered}%
\end{table}%

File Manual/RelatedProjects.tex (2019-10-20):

\chapter[Related OSS Projects]{Related OSS\\Projects}%
\label{c:rel_projects}%
This chapter looks at other projects from the open source software and open source hardware community which have the goal to develop their own 3D scanners\marginWarning[Important Notice]{It should be noted that the list of projects considered in this chapter does not claim to be exhaustive. In particular, there are various variations for the presented projects and the projects itself may already be a variation of an existing project.}. In some places comparisons to the Open3DScanner are given and influences that the projects have on the Open3DScanner are pointed out.%

In the sections~\ref{s:open_scan} and~\ref{s:3dTurn} other photogrammetry scanners are introduced while in the remaining sections 3D scanners based on other technologies are introduced.%

\section{OpenScan}%
\label{s:open_scan}%
First of all lets take a look at the project that had the biggest influence on the Open3DScanner, because it served as inspiration for it. The Open3DScanner is only an alternative realization of Thomas Megel's project:%

\hrefIdx{https://www.openscan.eu/}{OpenScan}%
\marginElement{\captionof{figure}{The OpenScan 3D Scanner}}%

OpenScan is based on automatically rotating the object to be scanned on two axes (X and Z) while automatically shooting the photos.%

The OpenScan project, like the Open3DScanner, relies on existing cameras that are connected to the scanner. One possibility that OpenScan offers, but was omitted from the Open3DScanner, is the usage of various SLR cameras for 3D scanning. The SLR camera is connected to the scanner via an infrared remote shutter which is connected to the scanner via an optocoupler. This option was removed for the Open3DScanner, because I don't own a SLR camera, nor do I plan to buy one. Furthermore, I am convinced that the quality of modern smartphone cameras is sufficient for the production of good quality 3D scans.%

A feature of the Open3DScanner that OpenScan does not provide is the possibility to connect LED lights directly to the 3D scanner and let the hardware control them during the scanning process.%

While there is no information about the applicable license on the project's homepage, the \hrefIdx{https://www.thingiverse.com/thing:3050437}{OpenScan Thingiverse project} indicates that the project is published under the CC-BY-NC 3.0 license.%

Scans with the OpenScan 3D Scanner are performed fully automatically after the settings for the respective scan have been selected. It is possible to configure how many images are taken per rotation of the z-axis and by which angle the scanner should rotate on the x-axis. In addition, it is possible to determine at how many positions on the x-axis a stop should be made, which in turn results in a complete rotation of the z-axis.%

In addition, there is a setting to adjust the time the scanner stops for each photo. This is important to ensure that the camera can refocus if necessary and avoid blurry shots.%

\infoInfo{Note}{Although the Open3DScanner was developed on the basis of the OpenScan project, it is not a simple copy. After OpenScan motivated the development of the Open3DScanner, requirements were defined independently from the original project. All artifacts (3D models, firmware, BOM) were developed especially for the Open3DScanner.}%

\section{3D Scanner Turntable}%
\label{s:3dTurn}%
Another open source photogrammetry 3D scanner is the project 3D Scanner Turntable by Dave Clarke.%

\hrefIdx{https://www.hackster.io/daveclarke/3d-scanner-turntable-for-cell-phones-updated-64fdb8}{3D Scanner Turntable}%
\marginElement{\captionof{figure}{The 3D Scanner Turntable}}

It relies on the use of a smartphone camera and promises that only the filament costs (\SI[round-precision=2,round-mode=places,round-integer-to-decimal]{30}[\$]) will be incurred for the construction of the 3D scanner. In addition to the smartphone, matching headphones with buttons that allow the camera to be released are required.%

In order to achieve the goal of a 3D scanner that is as inexpensive as possible, the project does not use additional electronics that automate scanning. Instead, it is necessary for the user to turn a crank that rotates the object to be scanned and ensures that the smartphone takes 55 photos every full turn.%

Unlike the Open3DScanner or the OpenScan, the object is only rotated on one axis during the scan, so it may be necessary to perform several scans and reposition the object each time. It is therefore necessary for the user to interact more strongly with the 3D scanner during use, but this is the only way to keep costs so low compared to other projects.%

As with the OpenScan project, the captured images must then be processed with appropriate software in order to obtain a 3D model.%

\section{Ciclop}%
The Ciclop 3D Scanner is an ambitious project of Jesús Arroyo, published by bq and based on laser triangulation. In addition to the 3D scanner itself, the project also provides its own software (Windows, Linux, and Mac OS X) for performing the 3D scans.%

\hrefIdx{http://diwo.bq.com/en/einfuhrung-ciclop-und-horus/}{Ciclop}%
\marginElement{\captionof{figure}{The Ciclop 3D Scanner}}%

Even though this project has no influence on the development of the Open3DScanner, it shall be introduced briefly here, as it is a wonderful open source hardware project for the creation of a 3D scanner, which provides detailed source information and documentation.%

The result of a scan is a point cloud, which has to be converted into a 3D model with other software (e.g. \hrefIdx{https://www.blender.org/}{Blender}) before the model can be used further, e.g. for 3D printing.%

The whole project is published under the CC-BY-SA 3.0 license as well as the GPL v2.%

Unlike the previous projects, the Ciclop is not based on external hardware (like the camera of a smartphone), but is a complete project in itself, requiring only a PC for operation.%

The core of the project is formed by a \hrefIdx{https://www.logitech.com/en-us/product/hd-webcam-c270}{Logitech C270 HD webcam} for creating the photos and two class 1 lasers, which are used to sample the object. The object to be scanned is positioned on a plate which is automatically rotated.%

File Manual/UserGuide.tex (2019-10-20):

\chapter{User Guide}
\label{c:userGuide}
This chapter describes how to use the fully assembled Open3D scanner to create 3D scans. First, the menu navigation of the Open3DScanner is explained and then the handling of the hardware.%

\section{Menu Navigation}%
If the Open3DScanner is switched on, the user sees the main menu on the display. It contains three sub-items which lead to the menus described in the following sections. The navigation within the menu is done by the knob to the right of the display. If it is rotated, the cursor position changes or the currently selected value is changed. To confirm a selection, press the knob.%

\subsection{Scan}%
The user has two options for starting a scan: Using a preset or creating a custom scan.%

The presets are predefined scan settings that allow a quick and easy start of the scan.%

If a custom scan is selected, the user must successively specify a series of settings that define the characteristics of the subsequent scan. The selected values are persisted and selected as default values for the next custom scan. This is done under the assumption that similar scans are frequently performed.%

First, the user must determine how many images are to be taken each time the turntable on which the object to be scanned is mounted is rotated. Any value between 1 and 3200 (inclusive) can be used. 3200 corresponds to the maximum resolution of the stepper motors at 200 steps per revolution and 1/16 microstepping.%

The next step is to select how far the turntable and the object are to be rotated on the x-axis during the scan. Any value between 1 and 359 (incluseive) degrees can be selected\marginInfo[Reasonable Values]{Even if there is a large range of values for the user to choose from, it often makes little sense to rotate the object further than 180 degrees around the x-axis. I usually use values in the range of 45 and 135.}.%

Finally, the number of steps in which the rotation on the x-axis is divided must be selected. Each step corresponds to a complete rotation of the turntable with the initially selected number of steps. The value range always starts at 1 and has a maximum value that corresponds to the maximum resolution of the stepper motor for the previously selected rotation around the x-axis.%

After all these parameters have been selected, the user is presented with a summary containing all selected values, the resulting number of images and the duration of the scan. At this point the scan can either be confirmed or aborted. When a preset is selected, the summary is presented directly to the user.%

Before the actual scan is started, it must be selected whether the lights of the Open3DScanner are to be switched on or off during the scan. The user is now prompted via the display to position the used smartphone appropriately and (if not already done) to establish a Bluetooth connection with the scanner. The scan cannot be started until the necessary Bluetooth connection has been established. As soon as this has been done, the Turntable can be moved to the desired start position and the scan can be started via the knob.%

During scanning, the current progress is shown on the display. It shows the number of recorded images, their total number and the remaining time. If the Bluetooth connection to the smartphone is lost during the scan, the scan is interrupted and the user is prompted to re-establish the connection. If the knob is pressed during the scan, the scan can be aborted or resumed after confirmation.%

\subsection{Settings}%
The settings menu is divided into categories that group the individual settings.%

\subsubsection{Scan}%
In this setting menu, you can set how many milliseconds the scanner stops after a motor movement or after taking a photo. This is necessary to allow the camera to focus images, but also to prevent possible vibrations of the scanner from blurring the images.%

\subsubsection{Display}%
In addition to the option of switching the backlight for the display on or off, the contrast of the display can be adjusted here.%

\subsubsection{Camera}%
Here you can select which camera type will be used during the scan. This is important because the control of various devices is different. Currently iOs and Android devices are supported.%

\subsubsection{Steppers}%
This menu allows you to adjust the behavior of the stepper motors. The selected stepper motor moves 15° back and forth while the settings are adjusted. This makes changes directly visible.%

The direction of movement of the motors can be changed if necessary. In addition, it can be determined with how many RPM the motor should move, what the acceleration and deceleration curve should look like, and which maximum values should be used for acceleration and deceleration.%

\subsection{Debug}%
The debug menu contains options to test some features of the Open3DScanner. Currently it is possible to switch the connected lights on and off and to trigger the camera. The system does not check whether a Bluetooth connection is actually present, so this must be checked in advance on the connected device.%

\section{Hardware Handling}%
This section contains some information about the built scanner and the interaction with the device.%

\subsection{Object Mounting}%
For the scan it is necessary to attach the object to be scanned to the Turntable. The holes in the Turntable allow to fix the object with cable ties. But this can lead to artefacts in the scan, so I prefer to use adhesive putty which can be reused many times.%

\subsection{Scanner Adjustment}%
Depending on the size of the object to be scanned, it may be useful to adjust the height of the lights or the turntable. The parts have been designed to allow this. This makes it possible to move the rotation center of the x-axis near the center of the object to be scanned.%

Thus, depending on the object, it can be ensured that it is always in the field of view of the camera, which is important for the automatic creation of images.%

\subsection{Status LED}%
The Open3DScanner has a bi-color LED, which is used to indicate the state of the scanner. The different state are explained below.%

\begin{table}[ht!]%
	\begin{centered}%
		\rowcolors{2}{tableLineTwo}{tableLineOne}% specify rowcolors in tabularx style
		\begin{tabularx} {\linewidth} {>{\rowmac \hsize=1\hsize}X>{\rowmac \hsize=1\hsize}X>{\rowmac \hsize=1\hsize}X<{\clearrow}}%
			\tabularxHeader%
			LED & State & Note\\%
			The LED lights green & Running & The scanner is turned on and ready for user interaction.\\%
			The LED lights yellow & Scanning & The scanner is performing a scan.\\%
			The LED flashes green very slowly & Scan finished & A scan has been finished successfully.\\%
			The LED flashes yellow slowly & Scan will continue & An interrupted scan will be continued soon.\\%
			The LED flashes red fast & No connection & The Bluetooth connection has been lost during scanning.\\%
		\end{tabularx}%
		\caption{Different states of the status LED}%
	\end{centered}%
\end{table}%

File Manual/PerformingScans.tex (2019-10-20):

\chapter{Perform Scans}
\label{c:performingScans}
Even though I am not an expert in the field of photogrammetry, I have gathered some experiences which I would like to share here. The recommendations given in this chapter do not claim to be universally valid and are based on my individual experiences.%

\section{Lighting \& Surface}%
A uniform illumination of the object to be scanned improves the quality of the scans significantly. In addition, glossy and transparent objects are much harder to scan compared to matte objects. For this reason, such objects should be treated (if possible) so that they have a better surface for the scanner. This can be done, for example, by spraying the objects with chalk spray.%

\section{Camera Settings}%
Most smartphone cameras have several features that automatically improve image quality. These range from autofocus and automatic white balance to AI functions that adjust color schemes based on recognized image content. Even if these functions provide better snapshots in everyday life, they are detrimental to the goals of photogrammetry. These functions make it more difficult to combine the images, which results in poorer scans.%

For this reason, the functions should be deactivated as far as possible and photos should be taken with fixed settings. This is especially true for color temperature, auto white balance, and autofocus.%

\section{Augmented Reconstruction}%
Since the object to be scanned must be attached to the turntable, an area of the object is always not visible on the captured images. This means that a single scan is not sufficient to scan an object completely. This may not be a problem for objects that have a flat base on which they stand and when no texture is required for that area.%

For many other objects this is a problem and multiple scans must be performed with different orientations of the object to capture the object from all sides.%

At least the software Meshroom has the function augmented reconstruction for this case. It allows to add another data set (an additional scan) to an existing data set (the first scan) and to calculate a new overall result. This can repeated as often as needed and results in a tree like structure of the Meshroom processing graph.%

That way it is often possible to create complete scans of objects. It may be necessary to filter some remaining artifacts of e.g. the Turntable of the reconstructed 3D model, but except from that you get a full scan and 3D model of the scanned object.%

This feature can also be used if the reconstructed model lacks details in some areas. Just perform an additional (detailed) scan of the respective area and start an augmented reconstruction.%

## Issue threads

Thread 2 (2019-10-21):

Change STEC12E08 Rotary Encoder a module

nazzrim, 2019-10-21:
A good candidate is the KY-040 rotary encoder module. It allows a better mounting of the rotary encoder.

In addition the arduino library used for interacting with the rotary encoder should be changed since the one currently used is very basic compared to others.

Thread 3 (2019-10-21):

Increase height of stands to provide a wider range of possible configurations.

nazzrim, 2019-10-21:
Right now not all holes on the rotorarm can be used to mount the turntable arm to the stands (at least when using a full size stepper motor), because the stands are not tall enough.

Closed 2019-10-25.

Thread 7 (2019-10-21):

Add some kind of endstop for auto-homing the scanner

nazzrim, 2019-10-21:
At this point the scanner is not aware of its motor positions at all.

Some kind of endstop (optical or mechanical) to get a defined orientation on the rotor (x-axis) would allow better movements.

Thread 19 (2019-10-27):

Add jumpers for microstepping

nazzrim, 2019-10-27:
Currently the microstepping is wired to 16th microstepping and cannot be changed.  Adding jumpers to the corresponding pins would allow to switch to different stepping modes.

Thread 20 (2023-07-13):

Decumentation chapter 2:  cheaper mechanical or by hand turntables

dosxga, 2023-07-13:
for chapter 2 there are cheaper mechanical or by hand turntables.  One such device is a cd/dvd pack of 50 case spindle.

nazzrim, 2023-07-13:
Thank you for your feedback. Please note that I am currently not working on this project anymore.

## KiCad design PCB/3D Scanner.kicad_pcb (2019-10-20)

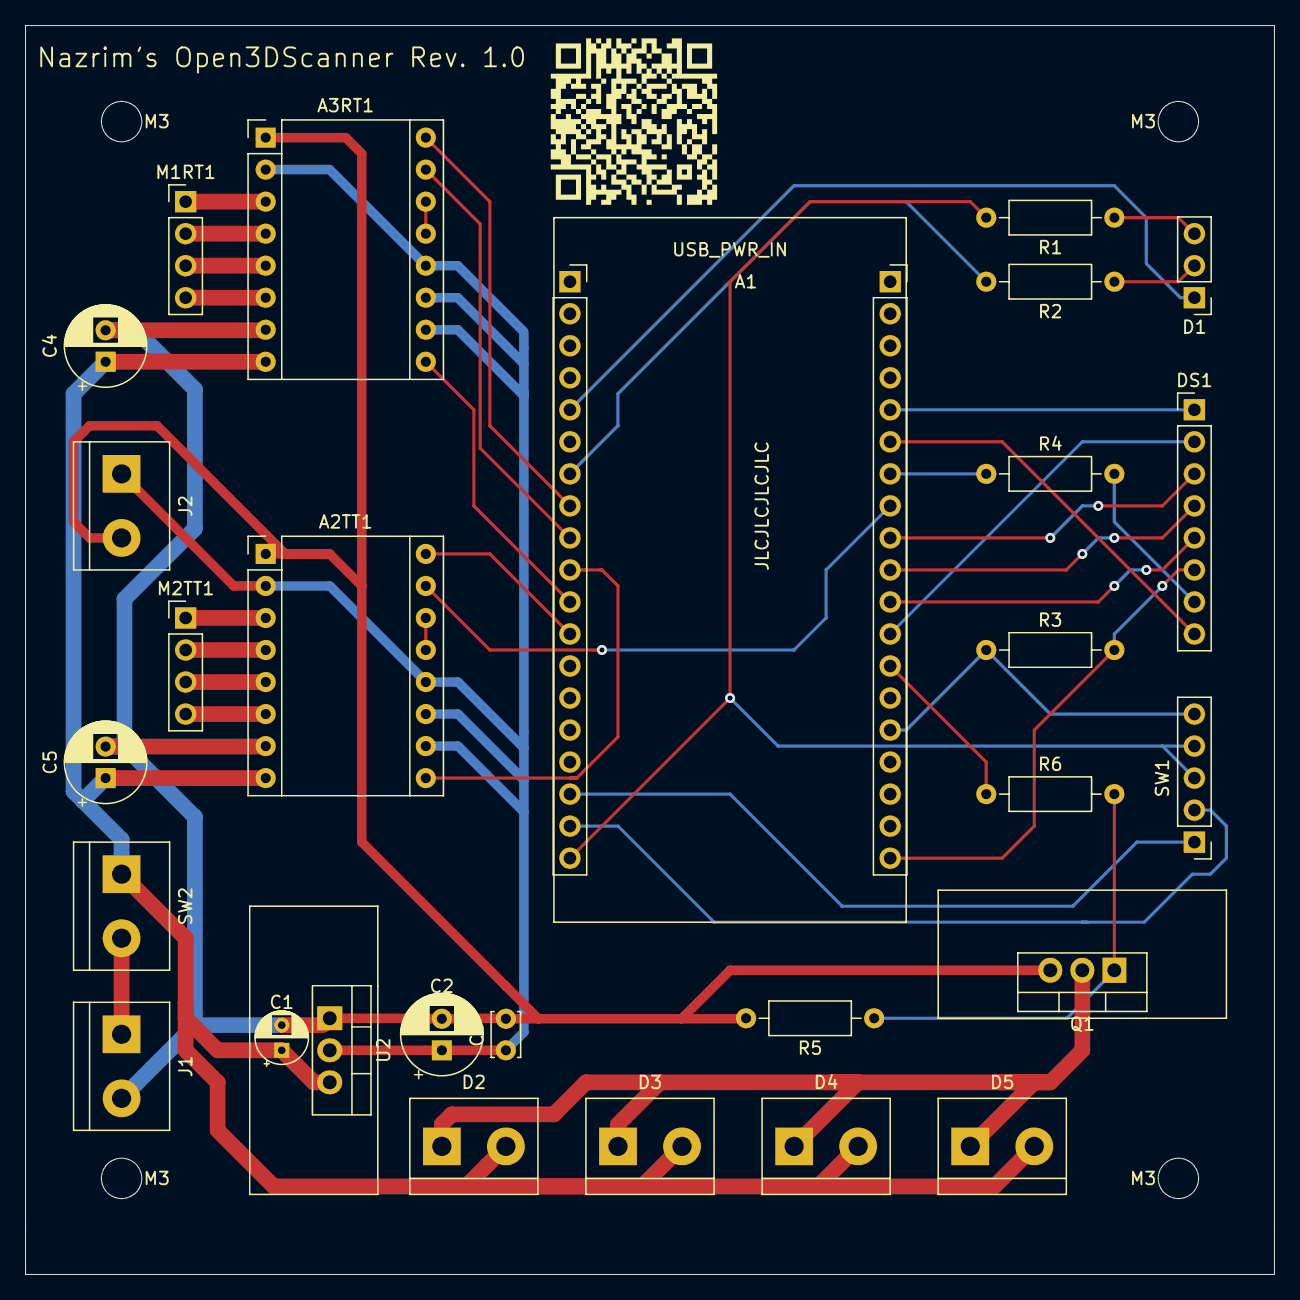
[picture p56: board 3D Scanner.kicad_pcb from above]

Board: 2 copper layers, 99.1 x 99.1 mm, 33 parts (0 on the bottom side), 40 nets.

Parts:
A1: AZDelivery-ESP32_NodeMCU
A2TT1, A3RT1: Pololu_Breakout_A4988; A4988
C1: 10μ; CP_Radial_D4.0mm_P2.00mm
C2, C4, C5: 100μ; CP_Radial_D6.3mm_P2.50mm
C3: 473n; C_Disc_D3.4mm_W2.1mm_P2.50mm
D1: LED_Dual_AAC; PinHeader_1x03_P2.54mm_Vertical
D2, D3, D4, D5: LED_Series; TerminalBlock_2_P5.08mm
DS1: Nokia5110-Display; PinHeader_1x08_P2.54mm_Vertical
J1: Barrel_Jack; TerminalBlock_2_P5.08mm
J2: Screw_Terminal_01x02; TerminalBlock_2_P5.08mm
M1RT1, M2TT1: Stepper_Motor_bipolar; PinHeader_1x04_P2.54mm_Vertical
M3, M3#2, M3#3, M3#4: M3; MountingHole_3.2mm_M3
Q1: IRLB8721PBF; TO-220-3_Vertical_Cooler
QR*****: QR-Code_MyMiniFactory_Profile
R1, R2, R6: 100; R_Axial_DIN0207_L6.3mm_D2.5mm_P10.16mm_Horizontal
R3, R5: 10k; R_Axial_DIN0207_L6.3mm_D2.5mm_P10.16mm_Horizontal
R4: 330; R_Axial_DIN0207_L6.3mm_D2.5mm_P10.16mm_Horizontal
SW1: Rotary_Encoder_Switch
SW2: SW_SPST; TerminalBlock_2_P5.08mm
U2: LT1086CT-5; TO-220-3_Vertical_Cooler

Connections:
+5V: A2TT1.2, A2TT1.10, A2TT1.11, A2TT1.12, A3RT1.2, A3RT1.10, A3RT1.11, A3RT1.12, C2.1, C3.1, J2.1, U2.2
+12V: A2TT1.8, A3RT1.8, C1.1, C4.1, C5.1, D2.2, D3.2, D4.2, D5.2, SW2.1, U2.3
/GREEN: A1.5, D1.1
/RED: D1.2, R2.1
GND: A2TT1.1, A2TT1.7, A3RT1.1, A3RT1.7, C1.2, C2.2, C3.2, C4.2, C5.2, J1.2, J2.2, Q1.3, R5.2, U2.1
unnamed: A1.7, R2.2
unnamed: A1.8, A3RT1.16
unnamed: A1.9, A3RT1.15
unnamed: A1.10, A2TT1.9
unnamed: A1.11, A3RT1.9
unnamed: A1.12, A2TT1.16
unnamed: A1.17, SW1.A
unnamed: A1.18, SW1.B
unnamed: A1.19, R1.2, SW1.C, SW1.S1
unnamed: A1.24, DS1.1
unnamed: A1.25, DS1.8
unnamed: A1.26, R4.1
unnamed: A1.27, A2TT1.15
unnamed: A1.28, DS1.3
unnamed: A1.29, DS1.4
unnamed: A1.30, DS1.5
unnamed: A1.31, DS1.2
unnamed: A1.32, R6.1
unnamed: A1.34, R3.1, SW1.S2
unnamed: A1.38, DS1.6, R3.2
unnamed: A2TT1.3, M2TT1.1
unnamed: A2TT1.4, M2TT1.2
unnamed: A2TT1.5, M2TT1.3
unnamed: A2TT1.6, M2TT1.4
unnamed: A2TT1.13, A2TT1.14
unnamed: A3RT1.3, M1RT1.1
unnamed: A3RT1.4, M1RT1.2
unnamed: A3RT1.5, M1RT1.3
unnamed: A3RT1.6, M1RT1.4
unnamed: A3RT1.13, A3RT1.14
unnamed: D1.3, R1.1
unnamed: D2.1, D3.1, D4.1, D5.1, Q1.2
unnamed: DS1.7, R4.2
unnamed: J1.1, SW2.2
unnamed: Q1.1, R5.1, R6.2

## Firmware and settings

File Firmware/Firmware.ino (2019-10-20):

#include <Arduino.h>                // Arduino
#include <EEPROM.h>                 // Arduino
#include <StackArray.h>             // Arduino
#include <BLEDevice.h>              // Arduino (https://github.com/nkolban/ESP32_BLE_Arduino)
#include <BLEUtils.h>               // Arduino (https://github.com/nkolban/ESP32_BLE_Arduino)
#include <BLEServer.h>              // Arduino (https://github.com/nkolban/ESP32_BLE_Arduino)
#include "BLE2902.h"                // Arduino (https://github.com/nkolban/ESP32_BLE_Arduino)
#include "BLEHIDDevice.h"           // Arduino (https://github.com/nkolban/ESP32_BLE_Arduino)
#include "HIDTypes.h"               // Arduino (https://github.com/nkolban/ESP32_BLE_Arduino)
#include "HIDKeyboardTypes.h"       // Arduino (https://github.com/nkolban/ESP32_BLE_Arduino)
#include <driver/adc.h>             // https://github.com/espressif/esp-idf
#include "soc/timer_group_struct.h" // https://github.com/espressif/esp-idf
#include "soc/timer_group_reg.h"    // https://github.com/espressif/esp-idf
#include <Nokia_LCD.h>              // https://github.com/platisd/nokia-5110-lcd-library
#include <A4988.h>                  // https://github.com/laurb9/StepperDriver
#include <ESP32Encoder.h>           // https://github.com/madhephaestus/ESP32Encoder/
#include <MenuSystem.h>             // https://github.com/jonblack/arduino-menusystem

/**
 * Begin of pin definitions
 */

/**
 * Free GPIOs:
 * - GPIO 0 (G0 - outputs PWM signal at boot)
 * - GPIO 3 (RX0 - HIGH at boot)
 */

 /**
  * Note: Because of the limited amount of GPIO Pins on the ESP32
  * the microstepping functionality is not used within the application.
  * Instead sixteenth microstepping is used by default for both steppers.
  * 
  * If in a future version a better solution is found the functionality
  * is added again. No code was removed, only outcommented.
  * 
  * If you want to ommit on some parts in favor of microstepping you can
  * return to the "old" state.
  * 
  * Relevant changes are in ESP32-3D_Scanner_-_Menu (microstepping submenues are not inserted into menu structure),
  * ESP32-3D_Scanner_-_Stepper-Rotor/Turntable (Microstepping function always returns sixteenth stepping and constructor
  * does not use microstepping pins anymore)
  */

// Pins used by the Nokia 5110 LCD Display
const uint8_t DISPLAY_RST = 13; // reset pin
const uint8_t DISPLAY_CE = 33;  // chip enable pin
const uint8_t DISPLAY_DC = 27;  // data/command selection pin
const uint8_t DISPLAY_DIN = 26; // serial input pin
const uint8_t DISPLAY_CLK = 25; // clock pin
const uint8_t DISPLAY_BL = 12; // background light pin

// Encoder pins used by Encoder STEC12E08
const uint8_t ENCODER_PHASE_A = 23; // bottom right pin
const uint8_t ENCODER_PHASE_B = 22; // bottom left pin
const uint8_t ENCODER_BUTTON = 34;  // top left pin

// Pins used by the A4988 driving the rotor stepper
//uint8_t ROTOR_MS1 = 15;
//uint8_t ROTOR_MS2 = 2;
//uint8_t ROTOR_MS3 = 4;
const uint8_t ROTOR_ENABLE = 18;
const uint8_t ROTOR_STEP = 17;
const uint8_t ROTOR_DIR = 16;

// Pins used by the A4988 driving the turntable stepper
//uint8_t TURNTABLE_MS1 = 5;
//uint8_t TURNTABLE_MS2 = 18;
//uint8_t TURNTABLE_MS3 = 19;
const uint8_t TURNTABLE_ENABLE = 5;
const uint8_t TURNTABLE_STEP = 14;
const uint8_t TURNTABLE_DIR = 19;

// Pins used by the bi-color status LED
const uint8_t STATUS_LED_GREEN = 2;
const uint8_t STATUS_LED_RED = 4;

// The transistor which switches light on/off needs a pin to drive the gate
const uint8_t LIGHT_SWITCH = 32;

// This is the number of scan presets defined in Scan.ino; information needed here since it is used in Menu.ino to build the correct menu structure
#define NUMBER_OF_SCAN_PRESETS 4

/**
 * End of pin definitions
 */

/**
 * Relevant data to keep track of the current application status.
 * Required for e.g. user input handling
 */
enum State {
  MENU,                                 // state for general menu navigation
  MENU_CHANGE_CONTRAST,                 // state for changing the contrast settings
  MENU_CHANGE_RPM_ROTOR,                // state for changing target RPM for rotor stepper
  MENU_CHANGE_ACCELERATION_ROTOR,       // state for changing acceleration for rotor stepper
  MENU_CHANGE_DECELERATION_ROTOR,       // state for changing deceleration for rotor stepper
  MENU_CHANGE_RPM_TURNTABLE,            // state for changing target RPM for turntable stepper
  MENU_CHANGE_ACCELERATION_TURNTABLE,   // state for changing acceleration for turntable stepper
  MENU_CHANGE_DECELERATION_TURNTABLE,   // state for changing deceleration for turntable stepper
  MENU_CHANGE_PHOTO_DELAY,              // state for changing the delay after a photo was taken
  MENU_CHANGE_MOVE_DELAY,               // state for changing the delay after a stepper was moved
  SCAN_CONFIGURE,                       // state for defining a custom scan
  SCAN_CONFIRM,                         // state for confirming chosen scan settings
  SCAN,                                 // state for scanning
};

// This is the current state of the application.
State current_state;

/**
 * This enum contains the valid microstepping values for the used A4988 drivers
 */
enum MicroStepping {
  FULL_STEP = 1,
  HALF_STEP = 2,
  QUARTER_STEP = 4,
  EIGHTH_STEP = 8,
  SIXTEENTH_STEP = 16
};

/**
 * Possible colors for the status LED.
 */
enum StatusLedColor : uint8_t {
  RED = 0,
  YELLOW = 1,
  GREEN = 2
};

/**
 * Possible blinking speeds for the status LED.
 */
enum StatusLedSpeed : uint8_t {
  SLOW = 0,
  FAST = 1,
  EXTRA_SLOW = 2
};

/**
 * The struct contains all settings which are required to perform a full scan.
 */
struct Scan {
  short photos_per_revolution;  // maximum "reasonable" value is rotor.microstepping * rotor.steps_per_revolution
  short rotation;               // maximum "reasonable" value is 360 since this setting is interpreted as degree value
  short rotation_divisions;     // maximum "reasonable" value is (rotor.microstepping * rotor.steps_per_revolution) / (rotation/360), while minimum value is 1 (start only)
};

/**
 * Scan presets are predefined scan objects with a name and scan settings which can be chosen from the menu.
 */
struct ScanPreset {
  char const* display_name;
  Scan preset;
};


// Used during MENU_CHANGE_CONTRAST state to store the current contrast value
uint8_t menu_change_contrast_current_value = 0;

// Used during MENU_CHANGE_CONTRAST state to store the current backlight state
uint8_t menu_change_contrast_backlight_state = 0;

// Used during ALL states which use the set min/max 12 bit function
unsigned short menu_set_min_max_12bit_value = 0;

// Used during ALL states which use the set 16 bit function
short menu_set_16bit_value = 0;

// This handle is used for task which run only a defined period of time and need to be deleted
TaskHandle_t rtos_task_handle = NULL;

// Actual lcd initialization can be found in Nokia5110-Display.ino
extern Nokia_LCD lcd;
// Can be found in Nokia5110-Display.ino
extern void initialize_display();

// Can be found in Encoder.ino
void encoder_button_isr();  

// Can be found in Stepper-Rotor.ino
extern A4988 stepper_rotor;
extern void initialize_stepper_rotor();

// Can be found in Stepper-Rotor.ino
extern float STEPPER_ROTOR_MIN_RPM;
extern float STEPPER_ROTOR_RPM_STEP_SIZE;
extern unsigned short STEPPER_ROTOR_MIN_ACCEL;
extern unsigned short STEPPER_ROTOR_ACCEL_STEP_SIZE;
extern unsigned short STEPPER_ROTOR_MIN_DECEL;
extern unsigned short STEPPER_ROTOR_DECEL_STEP_SIZE;

// Can be found in EEPROM.ino
extern const uint8_t EEPROM_STEPPER_ROTOR_RPM_POS;
extern const uint8_t EEPROM_STEPPER_ROTOR_RPM_MS_POS;
extern const uint8_t EEPROM_STEPPER_ROTOR_ACCEL_POS;
extern const uint8_t EEPROM_STEPPER_ROTOR_DECEL_POS;
extern const uint8_t EEPROM_STEPPER_ROTOR_ACCEL_DECEL_POS;


// Can be found in Stepper-Turntable.ino
extern A4988 stepper_turntable;
extern void initialize_stepper_turntable();

// Can be found in Stepper-Turntable.ino
extern float STEPPER_TURNTABLE_MIN_RPM;
extern float STEPPER_TURNTABLE_RPM_STEP_SIZE;
extern unsigned short STEPPER_TURNTABLE_MIN_ACCEL;
extern unsigned short STEPPER_TURNTABLE_ACCEL_STEP_SIZE;
extern unsigned short STEPPER_TURNTABLE_MIN_DECEL;
extern unsigned short STEPPER_TURNTABLE_DECEL_STEP_SIZE;

// Can be found in EEPROM.ino
extern const uint8_t EEPROM_STEPPER_TURNTABLE_RPM_POS;
extern const uint8_t EEPROM_STEPPER_TURNTABLE_RPM_MS_POS;
extern const uint8_t EEPROM_STEPPER_TURNTABLE_ACCEL_POS;
extern const uint8_t EEPROM_STEPPER_TURNTABLE_DECEL_POS;
extern const uint8_t EEPROM_STEPPER_TURNTABLE_ACCEL_DECEL_POS;
extern const uint8_t EEPROM_TIME_BETWEEN_PHOTO_LOW_POS;
extern const uint8_t EEPROM_TIME_BETWEEN_PHOTO_HIGH_POS;
extern const uint8_t EEPROM_TIME_AFTER_MOVE_LOW_POS;
extern const uint8_t EEPROM_TIME_AFTER_MOVE_HIGH_POS;

// Can be found in Menu.ino
extern void initialize_menu_structure();

// Can be found in State_Menu.ino
extern void menu_state_logic();

// Can be found in State-Menu-Change-Contrast.ino
extern void menu_change_contrast_state_logic();

// Can be found in State-Menu-Set-Min-Max-12Bit.ino
extern void menu_state_set_min_max_12bit_logic(
      const String affected_element,
      const String affected_setting,
      const bool use_float_values,
      const short min_short,
      const short step_short,
      const float min_float,
      const float step_float,
      const uint8_t store_address_a,
      const uint8_t store_address_b,
      const bool use_upper_bits);

/**
 * Begin of scroll multiplier values which are used in multiple locations.
 */


/**
 * Since there are 4096 different values some kind of scroll speed multiplier will help to make big adjustments.
 */
float scroll_speed_multiplier = 1.0;

/**
 * Counter how long no input was done. Required to reset the speed multiplier.
 */
uint8_t no_input_loops = 0;

/**
 * After how many frames without input the multiplier should be reset
 */
uint8_t multiplier_resetter = 6;

/**
 * Minimum scroll multiplier speed.
 */
float min_multiplier = 1.0;

/**
 * Maximum scroll multiplier speed.
 */
float max_multiplier = 10.0;

/**
 * This is a multiplier for the multiplier, and is used to increase the multiplier.
 */
float multplier_modifier = 1.16;

/**
 * End of multiplier flags.
 */

/**
 * Default arduino function. Will be called once on startup and is used to init
 * all subsystems.
 */
void setup() {
  // initialize serial connection for output printing
  Serial.begin(115200);

  // initialize all (hardware & software) subsystems
  initialize_light();
  initialize_status_led();
  initialize_EEPROM();
  initialize_BLE();
  initialize_display();
  initialize_stepper_rotor();
  initialize_stepper_turntable();
  initialize_encoder();
  initialize_scan();
  initialize_custom_scan();
  initialize_menu_structure();

  // application starts in menu state
  current_state = MENU;

  // start the main logic loop as freeRTOS task
  xTaskCreate(main_loop, "MainLoop", 20000, NULL, 5, NULL);
}

/**
 * The main logic loop will different logic functions depending on the current applications state.
 */
void main_loop(void*) {
  while (true) {
    // the BLE functionality seems to mess up interrupt handling.
    // therefore it is necessary to call this function here for proper user input handling.
    encoder_button_isr();
    // execute logic based on current application state
    if (current_state == SCAN_CONFIGURE) {
      scan_configure_state_logic();
    } else if (current_state == SCAN) {
      perform_scan();
    } else if (current_state == SCAN_CONFIRM) {
      scan_confirm_state_logic();
    } else if (current_state == MENU) {
      menu_state_logic();
    } else if(current_state == MENU_CHANGE_CONTRAST) {
      menu_change_contrast_state_logic();
    } else if(current_state == MENU_CHANGE_RPM_ROTOR) {
      menu_state_set_min_max_12bit_logic(
        "Rotor",
        "RPM",
        true,
        0,
        0,
        STEPPER_ROTOR_MIN_RPM,
        STEPPER_ROTOR_RPM_STEP_SIZE,
        EEPROM_STEPPER_ROTOR_RPM_POS,
        EEPROM_STEPPER_ROTOR_RPM_MS_POS,
        false);
    } else if(current_state == MENU_CHANGE_ACCELERATION_ROTOR) {
      menu_state_set_min_max_12bit_logic(
        "Rotor",
        "Acceleration",
        false,
        STEPPER_ROTOR_MIN_ACCEL,
        STEPPER_ROTOR_ACCEL_STEP_SIZE,
        0.0,
        0.0,
        EEPROM_STEPPER_ROTOR_ACCEL_POS,
        EEPROM_STEPPER_ROTOR_ACCEL_DECEL_POS,
        false);
    } else if(current_state == MENU_CHANGE_DECELERATION_ROTOR) {
      menu_state_set_min_max_12bit_logic(
        "Rotor",
        "Deceleration",
        false,
        STEPPER_ROTOR_MIN_DECEL,
        STEPPER_ROTOR_DECEL_STEP_SIZE,
        0.0,
        0.0,
        EEPROM_STEPPER_ROTOR_DECEL_POS,
        EEPROM_STEPPER_ROTOR_ACCEL_DECEL_POS,
        true);
    } else if(current_state == MENU_CHANGE_RPM_TURNTABLE) {
      menu_state_set_min_max_12bit_logic(
        "Turntable",
        "RPM",
        true,
        0,
        0,
        STEPPER_TURNTABLE_MIN_RPM,
        STEPPER_TURNTABLE_RPM_STEP_SIZE,
        EEPROM_STEPPER_TURNTABLE_RPM_POS,
        EEPROM_STEPPER_TURNTABLE_RPM_MS_POS,
        false);
    } else if(current_state == MENU_CHANGE_ACCELERATION_TURNTABLE) {
      menu_state_set_min_max_12bit_logic(
        "Turntable",
        "Acceleration",
        false,
        STEPPER_TURNTABLE_MIN_ACCEL,
        STEPPER_TURNTABLE_ACCEL_STEP_SIZE,
        0.0,
        0.0,
        EEPROM_STEPPER_TURNTABLE_ACCEL_POS,
        EEPROM_STEPPER_TURNTABLE_ACCEL_DECEL_POS,
        false);
    } else if(current_state == MENU_CHANGE_DECELERATION_TURNTABLE) {
      menu_state_set_min_max_12bit_logic(
        "Turntable",
        "Deceleration",
        false,
        STEPPER_TURNTABLE_MIN_DECEL,
        STEPPER_TURNTABLE_DECEL_STEP_SIZE,
        0.0,
        0.0,
        EEPROM_STEPPER_TURNTABLE_DECEL_POS,
        EEPROM_STEPPER_TURNTABLE_ACCEL_DECEL_POS,
        true);
    } else if(current_state == MENU_CHANGE_PHOTO_DELAY) {
      menu_state_set_16bit_logic(
          String("Photo Delay"),
          100,
          30000,
          EEPROM_TIME_BETWEEN_PHOTO_LOW_POS,
          EEPROM_TIME_BETWEEN_PHOTO_HIGH_POS);
    } else if(current_state == MENU_CHANGE_MOVE_DELAY) {
        menu_state_set_16bit_logic(
          String("Move Delay"),
          100,
          30000,
          EEPROM_TIME_AFTER_MOVE_LOW_POS,
          EEPROM_TIME_AFTER_MOVE_HIGH_POS);
    }
  }
}

/**
 * The default arduino loop is empty except of a delay since all functionality is handled with freeRTOS tasks.
 */
void loop() {
  delay(100);
}

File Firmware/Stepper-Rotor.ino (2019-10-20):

#include "soc/timer_group_struct.h"
#include "soc/timer_group_reg.h"
#include <A4988.h>

/**
 * The rotor stepper is used for rotating the scanned object around the x-axis.
 */

// gear ratio which is used to drive the rotor
float STEPPER_ROTOR_GEAR_RATIO = 40/8.0;

// rotor stepper's minimal RPM value
float STEPPER_ROTOR_MIN_RPM = 0.01;
// minimal difference between to RPM values for rotor stepper
float STEPPER_ROTOR_RPM_STEP_SIZE = 0.01;

// rotor stepper's minimal acceleration value
unsigned short STEPPER_ROTOR_MIN_ACCEL = 100;
// minimal difference between to acceleration values for rotor stepper
unsigned short STEPPER_ROTOR_ACCEL_STEP_SIZE = 1;

// rotor stepper's minimal deceleration value
unsigned short STEPPER_ROTOR_MIN_DECEL = 100;
// minimal difference between to deceleration values for rotor stepper
unsigned short STEPPER_ROTOR_DECEL_STEP_SIZE = 1;

// this is the number of steps the stepper needs for a full revolution
// typical values are 200 (1.8° stepper) and 400 (0.9° stepper)
short ROTOR_STEPS_PER_REVOLUTION = 200;

// The actual A4988 instance; microstepping disabled because the ESP32 offers not enough gpio pins for all functionality
A4988 stepper_rotor(ROTOR_STEPS_PER_REVOLUTION, ROTOR_DIR, ROTOR_STEP, ROTOR_ENABLE);//, ROTOR_MS1, ROTOR_MS2, ROTOR_MS3);

/**
 * Initialization of the rotor stepper loads all needed values from EEPROM
 * (RPM, microstepping, speedmode, acceleration, deceleration) and enables 
 * the motor.
 */
void initialize_stepper_rotor() {
  stepper_rotor.begin(load_stepper_rotor_rpm(), load_stepper_rotor_ms());
  stepper_rotor.setEnableActiveState(LOW);
  stepper_rotor.disable();
  update_stepper_rotor_speed_profile();
}

/**
 * Get the current RPM value for the rotor stepper.
 * The value is stored and EEPROM and is a combination of two bytes (one and a half to be more precise).
 */
float load_stepper_rotor_rpm() {
  // get rpm and ms settings from eeprom
  uint8_t rpm_byte = EEPROM.read(EEPROM_STEPPER_ROTOR_RPM_POS);
  uint8_t rpm_ms_byte = EEPROM.read(EEPROM_STEPPER_ROTOR_RPM_MS_POS);

  return STEPPER_ROTOR_GEAR_RATIO * STEPPER_ROTOR_MIN_RPM + (STEPPER_ROTOR_RPM_STEP_SIZE * (((rpm_ms_byte & 0x0F) << 8) | rpm_byte));
}

/**
 * Get the microstepping settings for the rotor stepper.
 * The value is stored in the upper half of a byte in EEPROM which is used for RPM settings.
 */
uint8_t load_stepper_rotor_ms() {
  // get ms settings from eeprom
  /*uint8_t rpm_ms_byte = EEPROM.read(EEPROM_STEPPER_ROTOR_RPM_MS_POS);

  if (bitRead(rpm_ms_byte, 4) == 1) {
    return HALF_STEP;
  } else if (bitRead(rpm_ms_byte, 5) == 1) {
    return QUARTER_STEP;
  } else if (bitRead(rpm_ms_byte, 6) == 1) {
    return EIGHTH_STEP;
  } else if (bitRead(rpm_ms_byte, 7) == 1) {
    return SIXTEENTH_STEP;
  }

  return FULL_STEP;*/
  return SIXTEENTH_STEP;
}

/**
 * Load the speed profile for the rotor motor from EEPROM.
 * The profile contains data about the speed type, acceleration and deceleration.
 */
void update_stepper_rotor_speed_profile() {
  // load EEPROM data
  uint8_t accel_byte = EEPROM.read(EEPROM_STEPPER_ROTOR_ACCEL_POS);
  uint8_t decel_byte = EEPROM.read(EEPROM_STEPPER_ROTOR_DECEL_POS);
  uint8_t accel_decel_byte = EEPROM.read(EEPROM_STEPPER_ROTOR_ACCEL_DECEL_POS);
  uint8_t bitmask = EEPROM.read(EEPROM_STEPPER_BITMASK_POS) & 0x0F;
  // create data for speed profile
  BasicStepperDriver::Mode speed_mode = (bitRead(bitmask, 0) == 1) ? stepper_rotor.LINEAR_SPEED : stepper_rotor.CONSTANT_SPEED;
  unsigned short accel = STEPPER_ROTOR_MIN_ACCEL + (STEPPER_ROTOR_ACCEL_STEP_SIZE * ((accel_decel_byte & 0x0F) << 8) | accel_byte);
  unsigned short decel = STEPPER_ROTOR_MIN_DECEL + (STEPPER_ROTOR_DECEL_STEP_SIZE * ((accel_decel_byte & 0xF0) << 4) | decel_byte);

  stepper_rotor.setSpeedProfile(speed_mode, accel, decel);
}

/**
 * This function will be executed as RTOS task if changes to the stepper configuration are applied.
 * It will periodically turn the stepper by 180 degrees into alternating direction.
 */
void stepper_rotor_debug_task(void*) {
  long rotate_degrees = 15;
  stepper_rotor.enable();
  while(true) {
    // start an asynchronous movement (triggering steps programatically is required)
    int8_t multiplier = (bitRead(EEPROM.read(EEPROM_STEPPER_BITMASK_POS), 1) == 0) ? 1 : -1;
    stepper_rotor.startRotate(multiplier*rotate_degrees * STEPPER_ROTOR_GEAR_RATIO);
    rotate_degrees *= -1;
    unsigned int wait_time = stepper_rotor.nextAction();
    while (stepper_rotor.getStepsRemaining() > 0) {
      // reset the watchdog manually since delayMicroseconds does not do it
      TIMERG0.wdt_wprotect=TIMG_WDT_WKEY_VALUE;
      TIMERG0.wdt_feed=1;
      TIMERG0.wdt_wprotect=0;
      // wait till next action needs to be executed
      delayMicroseconds(wait_time);
      // execute next action
      wait_time = stepper_rotor.nextAction();
    }
    vTaskDelay(250);
  }
}

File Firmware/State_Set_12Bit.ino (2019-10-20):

/**
 * This is the logic for a menu state that is used for different situation.
 * It allows to set a 12 bit value for short and float values.
 * Minimum, maximum and current value are displayed.
 * Since 12 bit are 1.5 bytes the user can define if the upper or lower half of the second byte will be used.
 */

// The actual definition can be found in Menu.ino
extern MenuSystem menu_system;

// Encoder initialization can be found in Encoder.ino
extern ESP32Encoder encoder;

// Encoder button initialization can be found in Encoder.ino
extern volatile boolean encoder_button_pressed;

/**
 * Logic function for this state handles user input to navigate the menu which is displayed on the lcd.
 * In theory all 12 bit values with type float or short are supported. If a new value should be made
 * changeable by this function some code changes are required since the application of the new value
 * after a change is hard coded right now.
 * 
 * @param affected_element Name of the element which uses the affected setting
 * @param affacted_setting Name of the actual setting which is adjusted now
 * @param use_float_values True if the altered setting is a float value, false if it is a short value
 * @param min_short Minimal value if short values are used
 * @param step_short Minimal difference between to values if short values are used
 * @param min_float Minimal value if float values are used
 * @param step_float Minimal difference between to values if short values are used
 * @param store_address_a EEPROM address where bits 0 to 7 are stored
 * @param store_address_b EEPROM address where bits 8 to 11 are stored
 * @param use_upper bits True if bits 8 to 11 should be stored in bits 4 to 7 of store_address_b, false for target bits 0 to 3
 */
void menu_state_set_min_max_12bit_logic(
      const String affected_element,
      const String affected_setting,
      const bool use_float_values,
      const short min_short,
      const short step_short,
      const float min_float,
      const float step_float,
      const uint8_t store_address_a,
      const uint8_t store_address_b,
      const bool use_upper_bits) {
  // process inputs
  // the encoder button has higher precedence than the encoder rotation
  if (encoder_button_pressed) {
    uint8_t lower_byte = menu_set_min_max_12bit_value & 0xFF;
    uint8_t upper_bits = (menu_set_min_max_12bit_value >> 8) & 0x0F;
    if (use_upper_bits) {
      upper_bits = (upper_bits << 4) | (EEPROM.read(store_address_b) & 0x0F);
    } else {
      upper_bits = (upper_bits) | (EEPROM.read(store_address_b) & 0xF0);
    }
    EEPROM.write(store_address_a, lower_byte);
    EEPROM.write(store_address_b, upper_bits);
    EEPROM.commit();
    consume_encoder_button();
    current_state = MENU;
  } else if ((int32_t)encoder.getCount() != 0) {
    menu_set_min_max_12bit_value += (short) (encoder.getCount() * scroll_speed_multiplier);
    // prevent over- and underflows
    if (menu_set_min_max_12bit_value > 4095) {
      if ((int32_t)encoder.getCount() > 0) {
        menu_set_min_max_12bit_value = 4095;
      } else {
        menu_set_min_max_12bit_value = 0;
      }
    }
    // reset encoder
    encoder.setCount(0);
    // adjust the multiplier for the next loop
    no_input_loops = 0;
    scroll_speed_multiplier = min(scroll_speed_multiplier * multplier_modifier, max_multiplier);
    // set the new value depending on the current applications state
    if(current_state == MENU_CHANGE_RPM_ROTOR) {
      stepper_rotor.setRPM(STEPPER_ROTOR_GEAR_RATIO * min_float + (menu_set_min_max_12bit_value * step_float));
    } else if(current_state == MENU_CHANGE_ACCELERATION_ROTOR) {
      stepper_rotor.setSpeedProfile(stepper_rotor.getSpeedProfile().mode, min_short + (menu_set_min_max_12bit_value * step_short), stepper_rotor.getDeceleration());
    } else if(current_state == MENU_CHANGE_DECELERATION_ROTOR) {
      stepper_rotor.setSpeedProfile(stepper_rotor.getSpeedProfile().mode, stepper_rotor.getAcceleration(), min_short + (menu_set_min_max_12bit_value * step_short));
    } else if(current_state == MENU_CHANGE_RPM_TURNTABLE) {
      stepper_turntable.setRPM(min_float + (menu_set_min_max_12bit_value * step_float));
    } else if(current_state == MENU_CHANGE_ACCELERATION_TURNTABLE) {
      stepper_turntable.setSpeedProfile(stepper_turntable.getSpeedProfile().mode, min_short + (menu_set_min_max_12bit_value * step_short), stepper_turntable.getDeceleration());
    } else if(current_state == MENU_CHANGE_DECELERATION_TURNTABLE) {
      stepper_turntable.setSpeedProfile(stepper_turntable.getSpeedProfile().mode, stepper_turntable.getAcceleration(), min_short + (menu_set_min_max_12bit_value * step_short));
    }
  } else {
    if (no_input_loops++ >= multiplier_resetter) {
      scroll_speed_multiplier = min_multiplier;
    }
  }
  // draw screen
  lcd.clear(false);
  // construct and draw title line
  String title = "Change " + affected_element;
  if (title.length() <= 16) {
    lcd.setCursor((84 - (title.length() * 5)) / 2, 0);
  }
  lcd.println(title.c_str());
  // constuct and draw second title line
  if (affected_setting.length() <= 16) {
    lcd.setCursor((84 - (affected_setting.length() * 5)) / 2, 1);
  }
  lcd.println(affected_setting.c_str());
  // draw min/max "title" - x-offset= (halfscreen (4px mid separation) - 4 characters) / 2 --> (40 - 20) / 2
  // for second entry 44 needs to be added
  lcd.setCursor(10, 2);
  lcd.print("Min:");
  lcd.setCursor(54, 2);
  lcd.print("Max:");
  // draw min and max values
  String min_str;
  String max_str;
  String current_value;
  if (use_float_values) {
    min_str = String(min_float, 2);
    max_str = String(min_float + (4095 * step_float), 2);
    current_value = String(min_float + (menu_set_min_max_12bit_value * step_float), 2);
  } else {
    min_str = String(min_short);
    max_str = String(min_short + (4095 * step_short));
    current_value = String(min_short + (menu_set_min_max_12bit_value * step_short));
  }
  lcd.setCursor((40 - (min_str.length() * 5)) / 2, 3);
  lcd.print(min_str.c_str());
  lcd.setCursor(44 + (40 - (max_str.length() * 5)) / 2, 3);
  lcd.print(max_str.c_str());
  // draw current value title and value itself
  lcd.setCursor(22, 4);
  lcd.print("Current:");
  lcd.setCursor((84 - (current_value.length() * 5)) / 2, 5);
  lcd.print(current_value.c_str());
  
  // sleep some time for (better) visibility on screen
  delay(TIME_BETWEEN_FRAMES);
}

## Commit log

2019-10-20 Added STLs
    [Backplate-Holder_v1.stl, Cable-Holder_v1.stl, Encoder-Holder_v1.stl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]
2019-10-20 Added KiCad Project for the PCB
    [3D Scanner-B_Cu.gbr, 3D Scanner-B_Mask.gbr, 3D Scanner-B_SilkS.gbr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]
2019-10-20 Added screenshots of spur gear generator settings
2019-10-23 Fixed scan UI issues
    [Scan.ino]
2019-10-25 Increased stand height by 5cm
    Rsolve #3
    [Passive-Stand_v1.stl, Rotor-Stand_v1.stl]
2019-10-25 Adjust Housing-Plate for Rev. 1.1
    [Housing-Plate_v1.stl]
2019-10-25 Fixed mixed up menu callbacks
    - When leaving the debug menu the light will be turned off
    [Menu.ino]
